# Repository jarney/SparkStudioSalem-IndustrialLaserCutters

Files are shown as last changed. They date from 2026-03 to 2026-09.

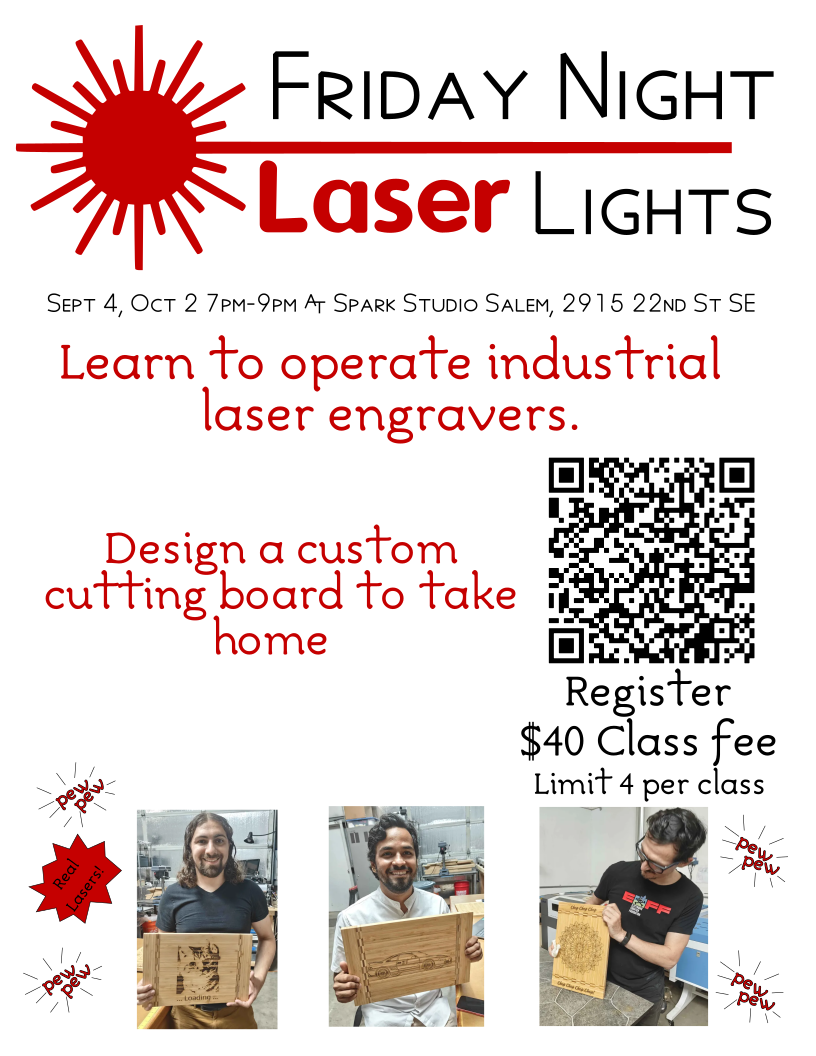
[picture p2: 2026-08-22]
promotional/FridayNightLaserLightsPromo1.png

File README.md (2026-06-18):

# Industrial 6090 150Watt CO2 Laser Cutters

This repository collects information about the Industrial
scale CO2 laser cutters at Spark Studios including
policies, safety information, training materials and technical
information such as wiring diagrams.

# Training Presentations
If you want to learn how to use the machines, there are several
presentations aimed at getting people started and certified:
* [Introduction Training](Training-GeneralPublic.pdf) and [handouts](Training-GeneralPublic-Handout.pdf): This course is intended for the general public
  to use the machines UNDER SUPERVISION of authorized users.  The nominal cost
  for this training is a $20 donation to the club.  You will learn to use the
  machine for basic cutting and engraving operations.  This is an introduction, so you
  will learn how to use the machines, but you will not yet be an expert.  This course makes use
  of some [templates](templates/svg) and a [template customization tool](https://jarney.github.io/spark/laser-cutters-6090/svg-templates/) to create
  designs for cutting during the class.

* [Authorized User Training](Training-AuthorizedUsers.pdf): This course is intended for paying members.  You will
  increase your knowledge and the focus is on ensuring safe operation and reacting to emergency
  conditions.  You will be allowed to use the machines unsupervised.

* Certifier Training (coming soon):  This course is intended for advanced users.  You will learn
  about the machine internals, alignment procedures, and more advanced topics.

# Policies and procedures

This section covers the policies and procedures for operating the machines.

* Use of these machines is governed by the [Policies](policies.pdf).
* When running jobs, please follow the [Operations Checklist](operation-checklist.pdf)
* When running jobs, please fill out a sheet in the [Operation Log](operation-log.pdf)
* Different materials should be cut and engraved with various settings.  While you may
  need to experiment to get the best results, the [Feeds and Speeds](FeedsAndSpeeds.pdf) document
  gives good starting points for common materials.
* To achieve better surface finishes, please refer to the [Pro Tips](pro-tips.pdf)
* These [Signs](signs.pdf) should be placed on the machines in event of malfunction to alert
  other users and Spark Studio board members of malfunctions.

If you wish to revise the policies, please edit the corresponding
OpenOffice (.odt) files and review with the Spark Studio Board.
Once approved, a pull-request can be sent to request that the official
copies of the policies be updated.  Note when revising policies, the
revision number and date MUST be updated in order to keep track
of which policy revision is the most recent.

# Technical Information

This section contains technical information for maintenance and
diagnosis of problems.  These are indended only for those tasked
specifically with maintaining and repairing the machines.  These
should not be used during normal operation.

This [operation manual](Gweike-operation-manual.pdf) covers
the use and operation of a similar laser cutter from Gweike.
While the laser cutters are not exactly this model, they
do give useful guidance on the machines and their operation.

The 6090 laser cutters are built using a Ruida controller
which interprets the GCode to guide the machine through making
cuts.  The [Ruida controller's documentation](RDC6445G-Control-System-V1.2-Manual.pdf)
describes more about its design and usage.

In addition, the [laser power supply has accompanying documentation](LASERPOWERSUPPLY欧规_1729590679720.pdf)
about its inputs and controls.

This [wiring diagram](laser-block-diagram.pdf) is
available for helping to understand the design of the
machines and general troubleshooting.  This diagram was produced
by reverse-engineering the design and is not authoritative,
but is as accurate as possible a diagram describing the wiring
of the machine based on its current configuration which has
been slightly altered from its original design.  The diagram is
authored in KiCad and future changes should be proposed and updated
using this format, reviewed, and implemented with the consent of
a Certifier or the Spark Studio Board.

# Modified Parts and accessories

Some parts have been designed and 3d printed in an effort to
improve the safety of the equipment.  These include:

* Spacers/stand-offs to hold a panel to prevent laser light from coming
  through the vent holes.
  
* Plugs for circular holes in front of Blue laser cutter.

* Holder for reed switch protecting the laser from firing with
  the door open.

The CAD for these files are maintained in this [FreeCAD file](LaserCutterParts.FCStd)
and printable versions can be found in the [STL](stl/) and [3MF](3mf/) directories.

# Alignment Procedures

The performance of the machines is highly dependent on how well
the machine is aligned.  Specifically, the optics must be aligned
closely with the gantry and the gantry needs to be square and parallel to
the bed.  Alignment of the machine is something of an art, but the
procedures are roughly outlined in the [Laser Alignment Guide](LaserAlignmentGuide.pdf).
These alignment procedures make use of some 3d-printed targets and
a [Laser Beam Alignment Worksheet](LaserBeamAlignmentWorksheet.svg) to assist in visualizing the beam path
and adjustments needed to bring the beam into the correct orientation.

There are beam target fixtures that can be inserted into the
apertures of [Mirror #2](stl/LaserCutterParts-P_AlignmentTarget_Mirror2.stl)
and [Mirror #3](stl/LaserCutterParts-P_AlignmentTarget_Mirror3.stl)
and affixed with blue painter's tape and marked using the [aperture](stl/LaserCutterParts-P_AlignmentTarget_ScribeAperture.stl) and [aperture](stl/LaserCutterParts-P_AlignmentTarget_Scribe.stl) marking jigs so that objective measurements can be made of beam position at each point in the beam path.

Source models for each of these parts can be found in
the [FreeCAD file](LaserCutterParts.FCStd) in case modifications to the models
are required.

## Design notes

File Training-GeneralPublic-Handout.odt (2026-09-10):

## Design:

- Open the template tool (First QR code on reverse)
- Choose a template and font.
- Use the “Customize” tab to customize to your liking.
- Preview the design to show the SVG that will be used for cutting.
- Share Design to save it as an SVG.
- Upload the SVG to the file server for cutting:

## Prepare for cutting:

- Move over to Lightburn PC
- Open Firefox and go to

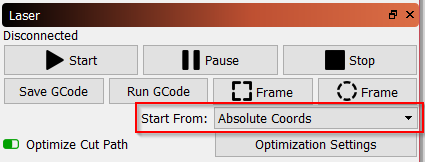
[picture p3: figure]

- http://vinyl.lan/
- Find your design in the uploads and download it to: Documents/Lightburn Projects/
- Open Lightburn from the Desktop
- File→Import, open your design from the imports folder
- Select all and align your design to X,Y at (60mm,60mm) to line it up with the jig using the icons on the toolbar.

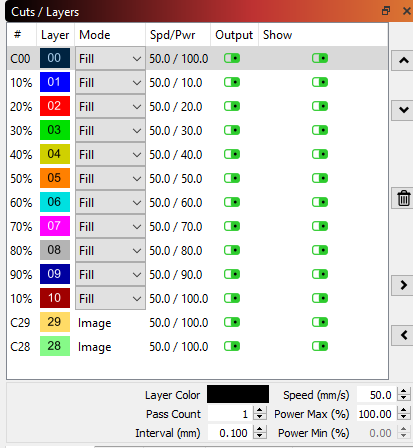
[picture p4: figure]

- Select Absolute Coordinates:
- Set the “Mode” and the “Speed/Power” for each of the colors
  - Images: Image mode, speed 250mm/s power 20%
  - Text (maroon): Fill or Line mode, speed 250mm/s power 20%
  - Lines (blue): Line mode, speed 250mm/s power 20%
  - Set the outermost line to turn off “Output”
- Confirm that “Cut Selected Graphics” is not turned on.
- Click “Send” button and give it a name (8 characters max)

## Perform the cut:

- Move over to laser cutter
- Place cutting board in jig, aligning it either “Portrait” or “Landscape” depending on your template.
- Use the “File” button and arrow keys on the laser cutter to select your file
- Press “Enter” to open up your file
- Press “Frame” button to draw the outline of your design and confirm it’s in the right place
- Confirm with your instructor that machine is ready to go (ventilation, chiller, power, air pump).
- Close door and press green “Start” button.
- Wait for machine to beep, do not leave unattended.

Other References

Other references that may be useful for making your own designs

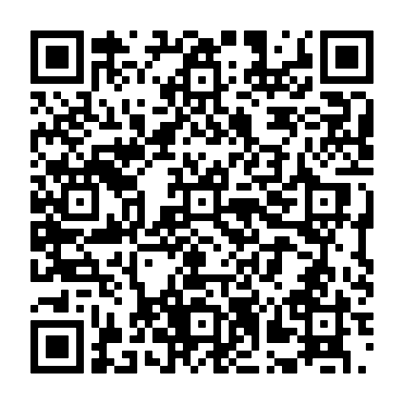
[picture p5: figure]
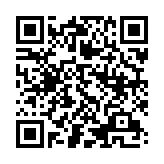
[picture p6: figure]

Spark Cutting Board Templates | Location to upload files for cutting | More Spark Studio Laser Resources

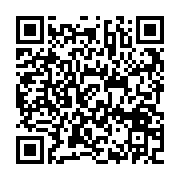
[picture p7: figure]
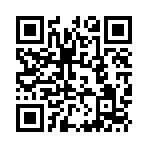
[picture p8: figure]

Inkscape Tutorials | Lightburn Tutorials

Intro to Laser Engraving (2/2)

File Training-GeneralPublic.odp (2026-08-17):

## Intro to Laser Engraving

Jon A 5/2/26

## Topics Covered

- Machine Basics
- Choose and customize a design
- Import into Lightburn for cutting
- We will set up cutter for operation
- You will laser etch your own cutting board to take home

## Machine Basics

- 150 Watt CO2 Laser (10.6um wavelength)
- Water cooled
- Adjustable bed height
- Usable Work Area: 550mm x 850mm (21.5in by 33.4in)
- Air extraction
- Air assist to improve cut quality/move debris away from nozzle

## Machine Basics

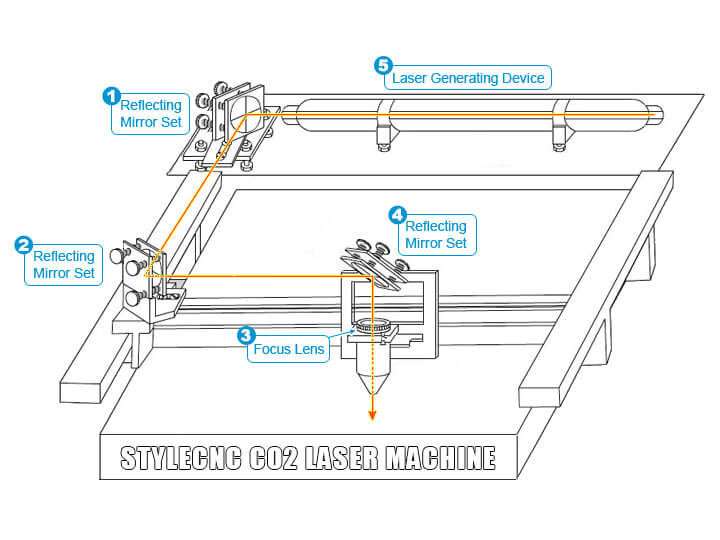
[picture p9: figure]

## Choose a template

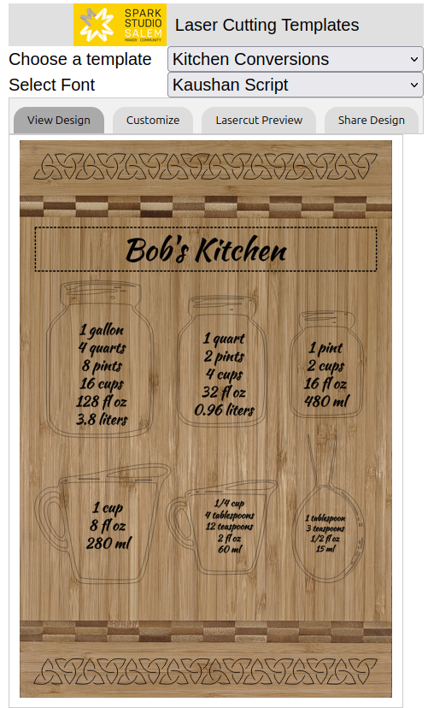
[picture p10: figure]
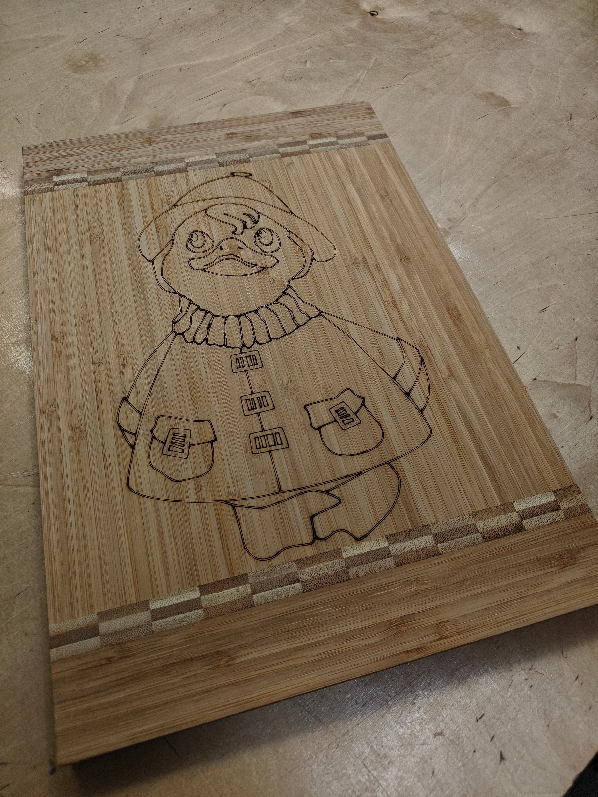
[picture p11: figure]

## Open template tool

- Select and customize file for cutting
- Download SVG file to save it
- Upload SVG file to cutting file server at:
- Lightburn for sending to laser

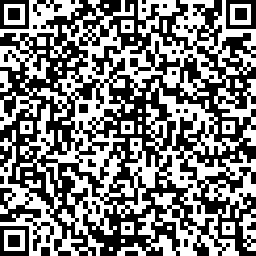
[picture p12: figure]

## Advanced Designs

- Inkscape is a great resource for more advanced designs
  - Free and open-source
- Other packages like Canva or Adobe Illustrator are suitable.
  - More expensive, but sometimes easier to use
- Great YouTube resources
- Check Handout for more information

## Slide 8

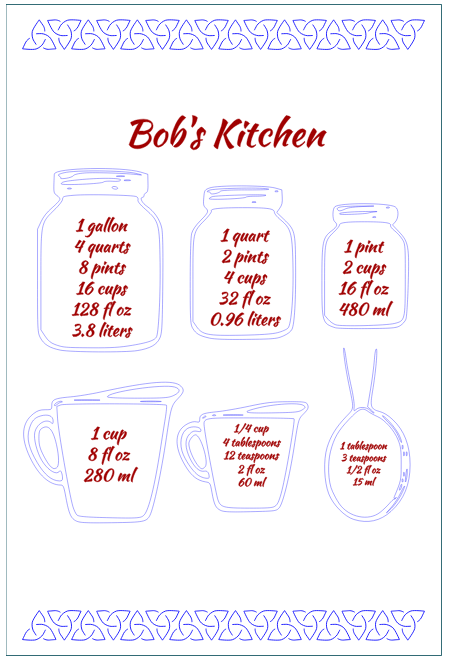
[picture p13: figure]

Finished Design

Design starts at 60mm, 60mm

Fits within the cutting board shape

Colors will be used to plan what type of operation the laser will perform.

## Import your design

- Go to Lightburn PC
- Download your SVG file
- Align design at x=60mm, y=60mm
- Matches physical location on machine

## Setting Feeds and Speeds

- Each element in your design should be given a “color”. That “color” will later determine how the cuts happen.
- Each color gets a “speed”, “power” and “mode”.
- Speed/Power determine how “deep” the laser will cut
- Mode determines how the cut is made

## Setting Feeds and Speeds

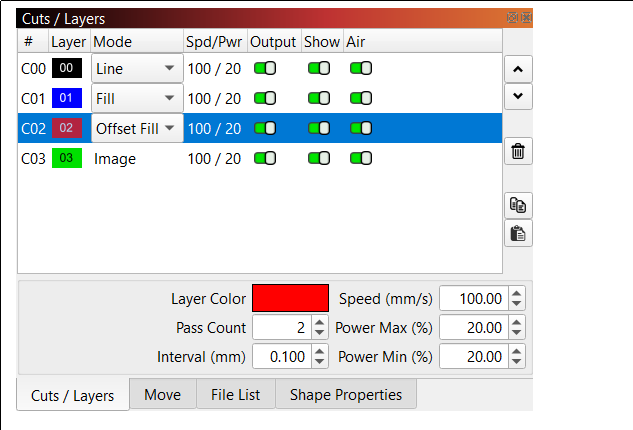
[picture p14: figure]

- Each “color” gets a speed and power, and mode
- Never exceed 50% power

## Modes

- Line: Simply follows the lines in a single pass
- Very thin lines sweeping across the design
- Good for line art and cutting shapes

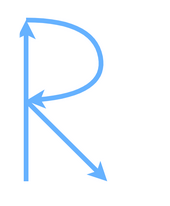
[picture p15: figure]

## Mode: Image

- Scans across the image line by line
- Pulses beam on and off to mark surface

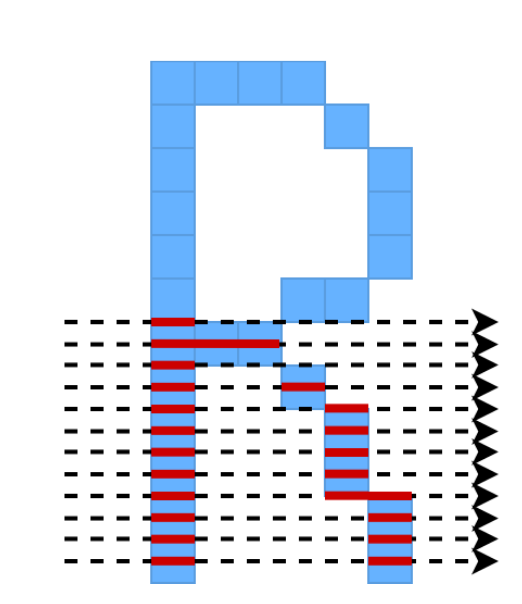
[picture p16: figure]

## Mode: Fill, Offset Fill

- Same as image, but used to fill in regions
- Offset fill doesn’t scan line by line, but instead repeatedly traces lines in concentric patterns to fill

## Material Library

- Assign layers (colors).
- Each one is a pre-set speed, power, and mode.
- Allows us to quickly determine how it will cut.
- You can still “fine-tune” speed and power afterwards if you want.

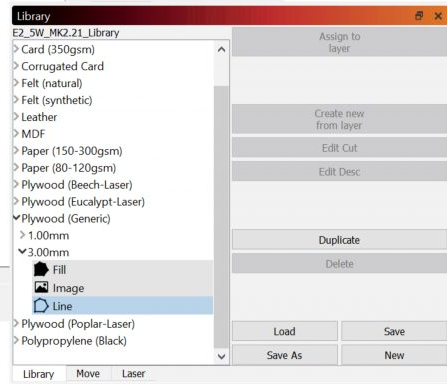
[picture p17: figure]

## Send to machine for cutting

- Once speed and power are set, we can send our design to the machine to cut it.
- SEND button
- Set “Start From” to “Absolute” coordinates


## Making the cuts

- Put material in machine
- Set focal distance between work and laser head to 5mm
- Close all doors/panels.
- Select File
- Press “Frame” button to confirm position
- Press green “Start/Pause” button.
- Don’t stare at beam
- Don’t leave unattended

## Materials

- Materials: Approved
  - MDF
  - All wood (except pressure-treated lumber)
  - Acrylic (Plexiglass)
  - UNTREATED or Vegan treated leather
  - Stone, Glass, Ceramic
  - Metal for surface engraving only
- Materials: Banned
  - Plastics containing chlorine
    - Vinyl, PVC, Nylon
  - Resins
  - Epoxies

## Safety

- Make sure all panels are closed
- Beware of fire, wood can burn.
- Beware in case lens vaporizes, possible Selenium exposure
- Do not touch mirrors or nozzle
- Persons under 18 must have parent or guardian nearby

## Next Steps

- After this training, feel free to come to the space during open-hours and use the machines provided that an authorized trainer is available to supervise machine operation. You will have to provide your own designs and materials, but use of the machines is free.
- If you become a member, there is additional training to:
  - Operate unsupervised or during non open-house hours.
  - Maintain and align machine
- If you enjoy this, we encourage you to become a member and get actively involved in the community.
- Tell your friends how much fun it is!

## Now, let’s go do some cutting!

- We will now move into the main space and make some cutting boards.
- Have fun with it and be creative.

## Next slides are just for reference

## Requirements

- Must be supervised by authorized user
- Must use only during office hours or open-house.
- 18+ or supervised by parent/guardian
- Donation to Spark
  - $40 Non-members
  - $20 Members
  - Please help us, it takes time and effort to keep these machines in good condition.
  - We also have to pay for facilities, electricity, etc.
  - You will not find a better deal anywhere!

## Trace bitmap to path

- OPTIONAL
- You can “convert” the image into a set of paths for better control
- Somewhat tricky to get the right effect, but can get really good results.
- Once it’s a path, you can edit nodes for very fine-grained control
- Works best when there’s a lot of contrast in the image

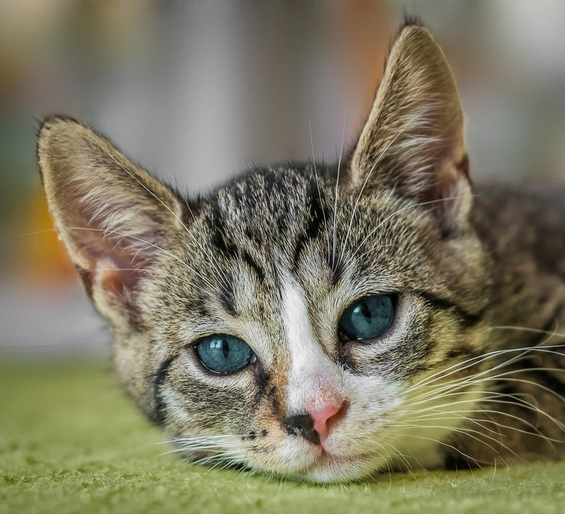
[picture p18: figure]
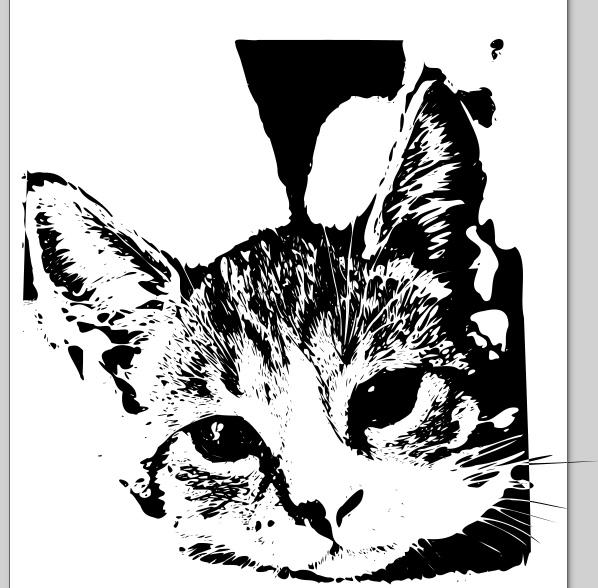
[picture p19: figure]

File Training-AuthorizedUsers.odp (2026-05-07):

## Laser Authorized User Training

Jon A 5/2/26

## Objectives

- Become an authorized user (able to use machines unsupervised)
- Learn normal operations procedures
- Learn safety procedures

## Requirements

- Must have passed “Intro” course
- Must be paying member
- Must agree to follow policy documents and checklist

## Policies

- You must carefully read, initial, and sign the policy document. This governs use of the machine and outlines your responsibility as operator.
- Copy provided by trainer
- Also available on GitHub, follow QR code on lasers.
- Policies (https://github.com/jarney/SparkStudioSalem-IndustrialLaserCutters/blob/main/policies.pdf)
- Yes, there will be a test.

## General Provisions

- Provide your own materials
- Not under influence
- Log use and failures or safety issues
- Keep machine locked when not in use
- Follow items on checklist

## Approved Materials

- If it’s not on the approved materials list, don’t cut it.
- If you disagree, get a copy of the Safety Data Sheet (SDS) and appeal to board for changes to policy, we can change if presented with a well-reasoned argument.

## Safety:

- Each type of safety condition should be handled depending on its nature.
  - Fire
  - Lens Vaporization
  - Tube Malfunction

## Fire

- Most common
- Not a problem if handled quickly
- Big problem if left unattended
- Use E-Stop
- Extinguish fire, escalating as needed
  - Turn off air assist
  - Use fire blanket
  - Use extinguisher
  - Call 911
- Log failure and notify board.

## Lens Vaporization

- Prevent by examining lens about monthly to make sure residue hasn’t accumulated. If you don’t want to clean it yourself, notify someone who can.
- Prevention is the most powerful tool here.
- Lenses cost ~$40 and it’s much easier, safer to replace a lens than to clean the machine.
- Keep lid closed
- Keep locked
- HAZMAT to avoid Selenium exposure
- Log failure and notify board
- Place sign on machine to warn of exposure.

## Laser tube malfunction

- Tube can crack
  - Physical shock
  - Water freezing
- High-voltage risk
- E-stop
- Log failure, notify board member
- Keep locked, closed
- Sign on machine

## Supervising others

- You may supervise general public WHO HAVE HAD INTRO TRAINING
  - We encourage this because it may help drive membership and donations
- You must watch them and stay nearby
- You are ultimately responsible for safety

## Demonstrate Safe Operation

- We will now go to the lasers and
  - Prepare them for use
    - Unlock machine
    - Exhaust vents
    - Fan power
    - Air assist
    - Chillers

## Demonstrate Safe Operation

- We will now go to the lasers and
  - Cut a small job
    - Focal length
    - Lightburn settings

## Demonstrate Safe Operation

- We will now go to the lasers and
  - Close them down
    - Lock machine
    - Exhaust vents
    - Fan power
    - Air assist
    - Chillers

## Examination

- Be prepared to answer questions about what to do in case of emergency
  - Fire
  - Lens vaporization
  - Tube malfunction

## Congratulations, you are now authorized

- Signoff
- Authorized user badge/token

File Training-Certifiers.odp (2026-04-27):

## Laser Certifier Training

Jon A 5/2/26

## Objectives

- Become a certifier
- Basic machine maintenance and diagnosis
- Deliver training
- Sign off on unsupervised use
- Question and “examine” candidates to make sure they understand safety.

## Requirements

- Must be a paying member
- Must agree to supervise and be responsible for use

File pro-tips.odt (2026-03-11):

Industrial Laser Cutter

Pro Tips

This is not an exhaustive list, but there are a few tips for achieving a better surface finish. Some experimentation may be required, but a quite good surface finish is possible with some setup and care.

Cast acrylic leaves a better surface finish and less deformation than extruded acrylic. If surface finish is important, use cast acrylic.

Higher pressure air assist removes residue from work piece more efficiently and leaves a better surface finish with less post-processing. If available, using an air compressor to feed the air assist will provide a better surface finish.

Flashback (reflections from the holders that scar the back of the work piece) can cause residue to form on the back/bottom of work piece. Consider using the “Slats” or a “pin bed” to hold the work piece in order to reduce flashover and leave a better surface finish on back.

When etching glass, the 150W lasers are usually too powerful. Use a low power setting and consider de-focusing the beam slightly. Also, applying a thin layer of dilute dish soap to work piece to facilitate cleaning of small glass particles formed during etching process.

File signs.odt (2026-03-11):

WARNING!

LASER HEAD IN NEED OF ALIGNMENT

HAZARD!

LENS VAPORIZATION

POTENTIAL SELENIUM EXPOSURE

DO NOT OPEN CABINET WITHOUT PPE

HAZARD!

LASER TUBE MALFUNCTION

POTENTIAL HIGH-VOLTAGE ELECTRICAL DISCHARGE

HAZARD!

MACHINE HAS EXPERIENCED UNCONTROLLED FIRE AND IS IN NEED OF MAINTENANCE

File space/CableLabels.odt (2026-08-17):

Network Cables

5G Router

Internet Ingress

See Network Diagram

5G Router to SW1

SW1

Ethernet Switch

See Network Diagram

SW1 to 5G Router

SW1 to SW2

Access Point 1

See Network Diagram

Access Point 1 to SW1 (PoE Port)

Access Point 2

See Network Diagram

Access Point 2 to SW2 (PoE Port)

SW2

Ethernet Switch

See Network Diagram

SW2 to SW3

SW2 to Access Point (PoE Port)

SW3

Ethernet Switch

See Network Diagram

SW3 to SW2

SW3 to Gweike Laser

SW3 to Blue Laser

ROUTER2

Internal Network

172.16.0.1 (hostname router)

See Network Diagram

Username: admin

Password: password

DHCP/DNS Server

172.16.0.2 (hostname dns)

OS Username: spark

OS Password: OS6and7

pihole password: OldSchool6and7s

DHCP Range: 172.16.0.100-172.16.0.254

Vinyl Cutter

172.16.0.3 (hostname vinyl)

Inkcut server for vinyl cutting using SVG

DNS Labels:

host:3dprint-octoprint1

ip:172.16.0.11

host:3dprint-qidi

ip:172.16.0.10

host:conference-roku

ip:172.16.0.81

host:digitalarts-inkjet-epson409961

ip:172.16.0.53

host:digitalarts-pc1-windows

ip:172.16.0.51

host:digitalarts-pc2-linux

ip:172.16.0.52

host:digitalarts-tshirt-power-tapo

ip:172.16.0.54

host:frontoffice-camera-wyse

ip:172.16.0.73

host:frontoffice-door-august

ip:172.16.0.191

host:frontoffice-pc

ip:172.16.0.71

host:frontoffice-windowbox

ip:172.16.0.70

host:frontoffice-printer

ip:172.16.0.72

host:laser-cutter-airsensor-electricimp

ip:172.16.0.25

host:laser-cutter-crackle

ip:172.16.0.23

host:laser-cutter-particlesensor-electricimp

ip:172.16.0.21

host:laser-cutter-pop

ip:172.16.0.24

host:laser-cutter-snap-glowforge

ip:172.16.0.22

host:laser-cutter-vinyl

ip:172.16.0.3

host:loft-camera-wyse

ip:172.16.0.91

host:loft-xbox-david-duncan

ip:172.16.0.90

host:network-accesspoint1-loft

ip:172.16.0.30

host:network-accesspoint2-3dprinting

ip:172.16.0.31

host:network-switch-netgear-gs728tp

ip:172.16.0.32

Breaker Labels

Breaker: B1 : Northwest Warehouse Plugs

Breaker: B3 : Bathroom

Breaker: B3 : Bathroom

Breaker: B3 : Bathroom

Breaker: B5 : Warehouse Heater

Breaker: B7 : Loft lights and network

Breaker: B9 : South Wall Plugs

Breaker: B11,B13 : 220VAC Under breaker panel

Breaker: B15,B17 : Mini-split AC unit

Breaker: B19 : Conference room

Breaker: B19 : Conference room

Breaker: B19 : Conference room

Breaker: B19 : Conference room

Breaker: B21 : East Wall “Pop” (Blue&White Laser cutter)

Breaker: B23 : East Wall “Crackle” (Gweike)

Breaker: B25 : Northeast Wall 3d printers, “Snap” GlowForge

Breaker: B27 : East Wall Electronics Bench

Breaker: B2 : Warehouse Lights

Breaker: B4, B6 : Water Heater

Breaker: B8 : Overhead Power Drop

Breaker: B10 : Outside Lights

Breaker: B12,B14 : Do not turn off/ Unknown(?)

Breaker: B16,B18 : Bathroom Heater

Breaker: B20,B22,B24 : Laser Exhaust Fans

Breaker: B26,B28,B30 : Air Compressor Panel

# PC Labels

General Purpose PCs

For use in training programs and general public:

Ubuntu 24.04LTS

Password: OS6and7

Loaded with:

Inkscape

Lightburn

Gimp

FreeCAD

A bunch of fonts

Please speak with Jeremy G, Jon A, or Rike S before making modifications

Please return to loft shelf when finished

Monitor for General Purpose PC

General Purpose PCs

Anyone may use these for training or general use.

Please return to this location when you are finished using them.

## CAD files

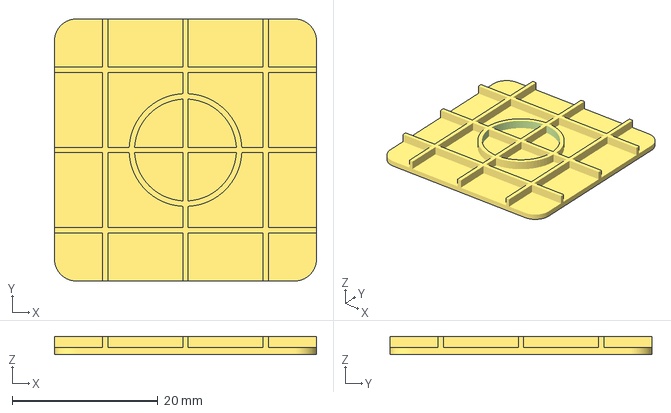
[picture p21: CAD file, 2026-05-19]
3mf/StampSurface.3mf
36.0 x 36.0 x 2.50 mm

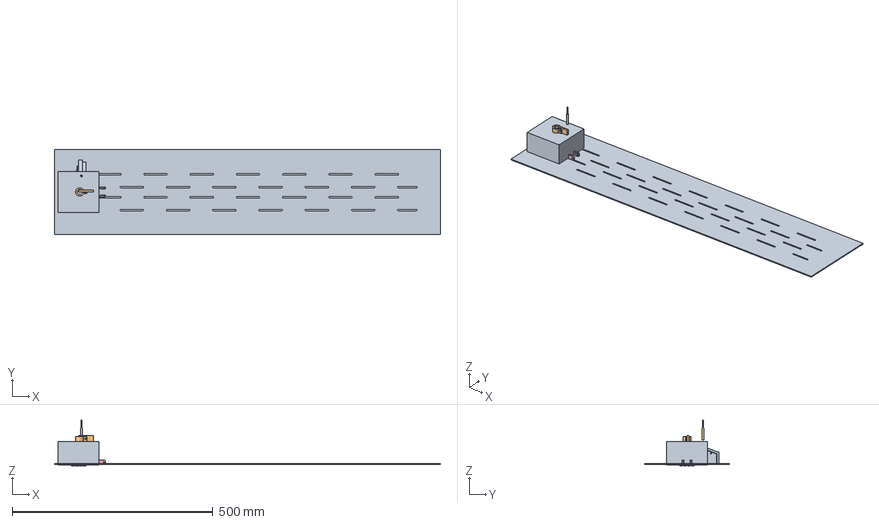
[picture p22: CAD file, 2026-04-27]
LaserCutterParts.FCStd
961.4 x 211.8 x 114.3 mm
B_FrontPanel
B_FrontPanelBaffle_Spacer
B_FrontPanelBaffle_Endcap
B_LimitSwitchSpacer
B_HolePlug_FrontPanels
B_HolePlug_Tester
B_ReedSwitch_Magnet
B_ReedSwitch_Holder
B_Cabinet_Body
B_Cabinet_Lid
B_ReedSwitch
B_CAMTest
B_TPLinkBracket_Right
B_TPLinkBracket_Left
B_AlignmentWrench1
B_AlignmentWrench2
B_AlignmentTarget_Mirror3
B_AlignmentTarget_Mirror2
B_HolePlug_SidePanels
B_AlignmentTarget_Stamp
B_AlignmentTarget_Scribe
B_IndicatorMount
B_AlignmentTarget_ScribeAperture
B_AlignmentTarget_HeadTube
B_AlignmentTarget_HeadTarget
B_LaserPointerMount
B_LaserPointerMountAperture
B_AlignmentTarget_Gweike_Mirror3
B_IndicatorMount2
Model-P_CAMTest
CutTool
SHAPESTRING_AlignmentTarget_Mirror3_Label001
Stock
5mm Endmill

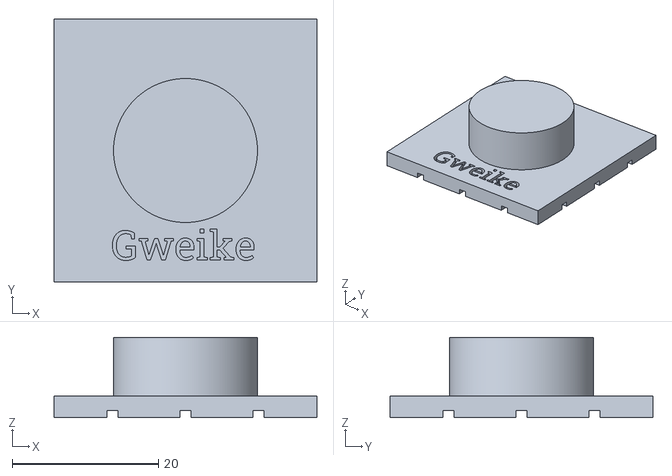
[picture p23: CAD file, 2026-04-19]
stl/LaserCutterParts-P_AlignmentTarget_Gweike_Mirror3.stl
36.0 x 36.0 x 11.0

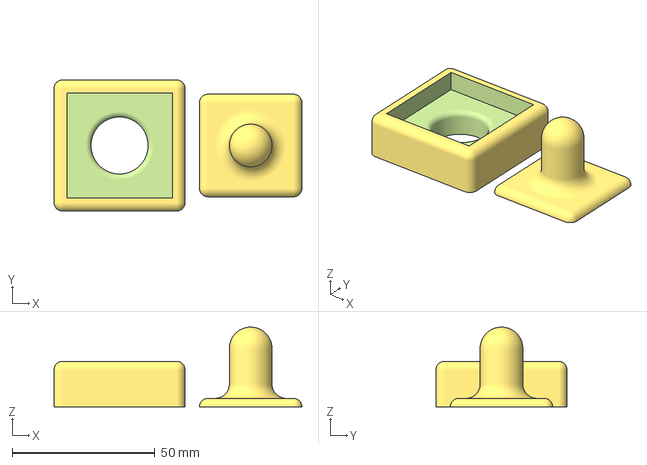
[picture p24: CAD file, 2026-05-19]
3mf/AlignmentStamp.3mf
87.0 x 46.0 x 28.0 mm

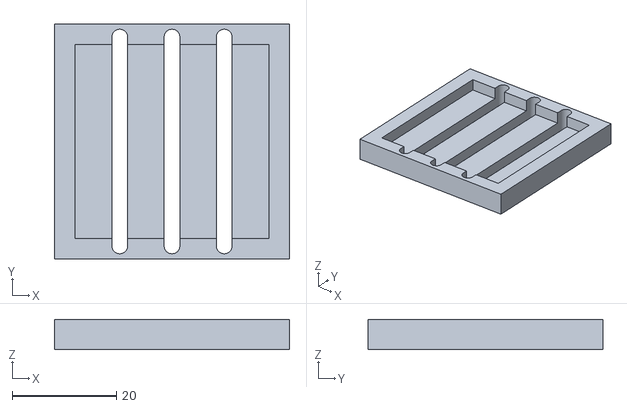
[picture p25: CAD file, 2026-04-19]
stl/LaserCutterParts-P_AlignmentTarget_Scribe.stl
45.0 x 45.0 x 5.80

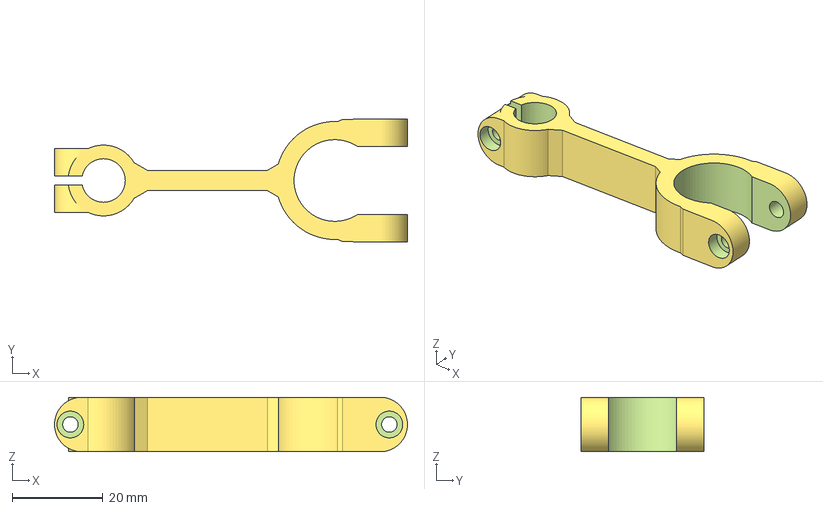
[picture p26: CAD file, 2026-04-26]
3mf/dial_holder.3mf
77.8 x 27.0 x 12.0 mm

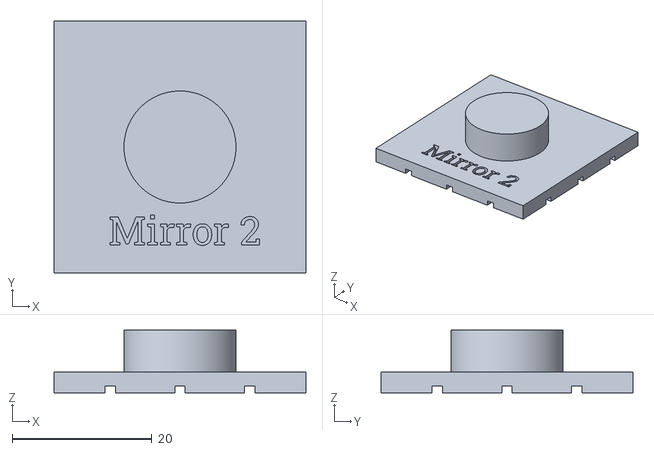
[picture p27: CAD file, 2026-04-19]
stl/LaserCutterParts-P_AlignmentTarget_Mirror2.stl
36.0 x 36.0 x 9.00

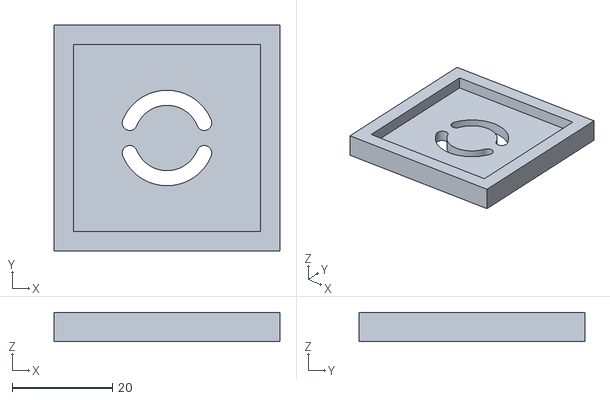
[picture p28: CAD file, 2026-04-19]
stl/LaserCutterParts-P_AlignmentTarget_ScribeAperture.stl
45.0 x 45.0 x 5.80

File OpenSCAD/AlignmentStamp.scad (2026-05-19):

include<BOSL2/std.scad>

shell = [46,46,16];
disc = [10,undef,8];
plate = [37,37,shell.z];
stamp = [36,36,1];
aperture = 14;
$fn = 72;

/* [Select] */
part = "set";  // [base, handle, set, stamp,set]

if (part == "base")   {base();}
if (part == "handle") {handle();}
if (part == "set")    {left(shell.x/2) base(); right(shell.x/2) handle();}  
if (part == "stamp")  {stamp();}   // print with softest available tpu


module base() {
    diff() {
        cuboid(shell, rounding = 3, except = BOT, anchor = BOT) {
            tag("remove") position(BOT){
                up(disc.z+1) cuboid(plate, anchor = BOT);
                cyl(h = disc.z+1.01, r = disc.x, rounding2 = -2, anchor = BOT);
            }
        }
    }
}

module stamp() {
    cuboid(stamp, rounding = 3, edges = "Z", anchor = BOT)
        position(TOP){
            xcopies(n=3, spacing = 11) cuboid([0.75,stamp.y,1.5], anchor = BOT);
            ycopies(n=3, spacing = 11) cuboid([stamp.x,0.75,1.5], anchor = BOT);
            tube(id = aperture, wall = 0.75, h = 1.5, anchor = BOT);
        }
}

module handle() {
    cuboid([stamp.x, stamp.y, 3], rounding = 3, edges = ["Z",TOP], anchor = BOT)
        position(TOP) cyl(h = 25, d = 15, rounding1 = -5, rounding2 = 7.5, anchor = BOT);
}

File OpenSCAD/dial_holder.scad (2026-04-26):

/*  Dial holder for Blue_6090 Industrial Laser Cutter Alignment
    Printing from Carbon or Glass Fiber filled filament recommended.
*/


include <BOSL2/std.scad>
include <BOSL2/screws.scad>

$fn = 72;
wall = 3;
zdim = 12;   // Overall height
d1 = 9.6;    // Dial Indicator Clamp Dia.
d2 = 18;     // Lens Barrel Clamp Dia.
bridge = [50-d1/2-d2/2-2*wall+2, 1.5 * wall, zdim];

holder();

module holder() {
    diff() {
        // Dial Indicator Clamp
        tube(id = d1, wall = wall, h = zdim, anchor = BOT){
            position(BOT) tag("remove") cyl(h = zdim, d = d1, anchor = BOT);
            position(LEFT) right(2*wall) cuboid([3*wall,4*wall+2,zdim], rounding=zdim/2, edges="Y", except=RIGHT, anchor=RIGHT){
                position(FWD) left(1) tag("remove") screw_hole("M3", l = 2*wall, head = "socket", anchor = TOP, orient=FWD);
                // Sized for m3 heat-set threaded insert
                position(BACK) left(1) tag("remove") ycyl(d = 4, l=2*wall, anchor = BACK);
            }
            position(LEFT) tag("remove") cuboid([4*wall, 2, zdim]);
            // Connecting Bar
            position(RIGHT) left(1) cuboid(bridge, anchor = LEFT){
                //End fillets
                align([LEFT,RIGHT], inside = true) tag("keep") left(wall*3/4+$idx*1.5*wall) zrot($idx*180) cyl(d = 3*wall, h = zdim, anchor = BOT, $fn = 3);
                // Lens Barrel Clamp
                position(RIGHT) left(1) tube(id = d2, wall = wall+1, h = zdim, anchor = LEFT){
                    position(BOT) tag("remove") cyl(h = zdim, d = d2, anchor = BOT);
                    align(RIGHT, inside = true, shiftout = 3) tag("remove") cuboid([4*wall+3,15,zdim+1]);
                    position(RIGHT) left(3*wall) cuboid([4*wall,15+4*wall,zdim], rounding= zdim/2, edges="Y", except=LEFT, anchor=LEFT){
                        align([BACK+LEFT, FWD+LEFT], inside = true, shiftout = -0.2) tag("keep") left(3) xscale(4) cyl(h = zdim, d = 1.4, $fn=6);
                        position(FWD) right(2) tag("remove") screw_hole("M3", l = 20, head = "socket", anchor = TOP, orient=FWD);
                        // Sized for m3 heat-set threaded insert
                        position(BACK) right(2) tag("remove") ycyl(d = 4, l=2*wall, anchor = BACK);
                    }
                }
            }
        }
    }


}

 //left(10) fwd(50) zrot(90) ruler();

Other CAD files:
stl/LaserCutterParts-P_AlignmentTarget_Mirror3.stl

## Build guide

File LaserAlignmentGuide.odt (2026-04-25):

Outline of procedures to align the gantry, optics, and bed

# Introduction

The performance of these laser cutters is highly dependent on how well the machine is aligned and calibrated. The alignment of the machine is something of an art and requires patience and understanding of the fundamentals of optics. Fortunately, if inspected regularly, the full procedure is rarely needed. This document contains an outline of the main alignment procedures and also a monthly maintenance guide. Once aligned, the machine should be maintained by following the monthly inspection process to verify that the machine is still adequately aligned and perform minor adjustments as needed. This is intended to ensure that the full alignment process is needed only rarely and that most of the time, only minor adjustments are needed to keep the machine in working order.

# Alignment Procedure Outline

## 1. Gantry Skew

In this stage, we aim to align the gantry so that the left and right rails are parallel. Using a bubble-level, check that each of the rails is angled from front-to-back by the same amount. If necessary, the entire machine can be trammed so that they are both level as closely as possible. Note that precise alignment is not necessary, but try to get the left and right rails within about 1 degree of the same angle front-to-back. The height of the front anchor point of each of the rails can be adjusted by loosening the screws holding the Y axis rails to the chassis and moving them higher or lower. Continue iterating on this until they are as close to parallel as you can make them. [Ref 1].

This is not too crucial for the optics because mirror #2 rides along the rails. Any “skew” in the yz plane will be washed out because the mirror moves with the rail. Nonetheless, make an effort to ensure that the rails are as level as possible in reference to one another.

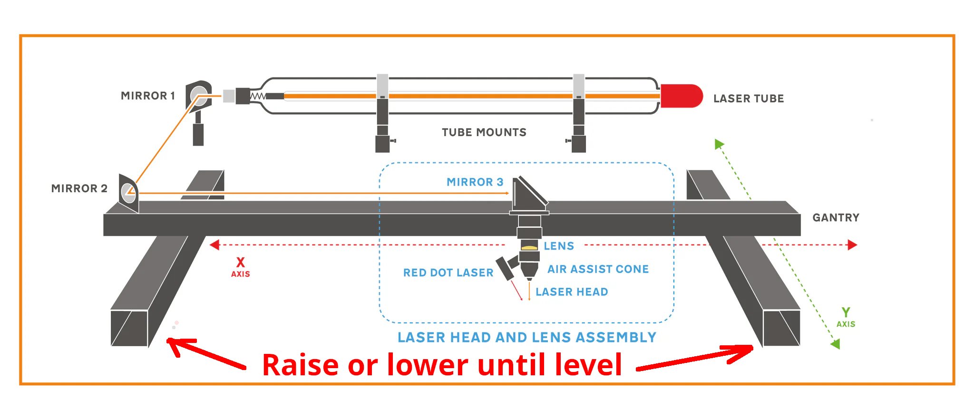
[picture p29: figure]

Measuring gantry skew. In order to check the gantry for skew, use a piece of fine thread stretched taught on the two diagonals of the gantry rails. If the gantry is square in the YZ plane, the two threads will intersect at the center. If one is higher or lower, then the rails are not perfectly parallel. Raise or lower the gantry until the two threads are just barely touching. You can secure the thread at each end with magnets or tape so they remain tight while making adjustments. Make sure to remove the thread after adjustment.

## 2. Gantry Mirror Interference

It sometimes happens that mirror #2 mounted on the gantry is accidentally bumped by the drag chain, cables, or other impediments. It only takes a microscopic deflection to move the mirror and thus beam spot at the far end of the machine. Take care to ensure that the cables, drag chain, and other moving parts do not bump or interfere with the free motion of the mirror mounted on the gantry.

## 3. Bed Leveling

In this stage, we aim to ensure that the XY plane of the bed is parallel to the XY plane of the gantry. The easiest way to do this is to place a large rigid, square object on the bed. Ideally, this object should be a) flat b) rigid, and c) cover the entire bed.

Next, jog the laser head to each of the 4 corners and use a small flat object to move the laser head so that the lowest of the 4 corners just touches the object. Our aim from here will be to adjust the z-axis lead screws so that all 4 corners match. To adjust one of the lead screws, use a hex wrench to loosen the set screw for the sprocket for that lead screw and manually adjust the lead screw until it just touches the object or the dial indicator reads the correct height. Re-tighten the set screw for the sprocket to lock the position in place. Continue this process until all 4 corners read the same height in reference to the tip of the laser tube.

For extra precision, a dial indicator can be mounted on the laser lens tube. Once done, the laser head can carefully be moved around the bed to measure how much deviation there is across the bed. A good alignment should yield something on the order of 10 thousandths of an inch (0.254mm)

This image depicts using a dial-indicator mounted on the laser lens aperture to measure relative height of the bed against the plane of the gantry. Note that the indicator SHOULD NOT BE MOUNTED UNTIL THE CONTROLLER HAS BEEN TURNED ON AND HOMED. You don’t want the indicator to be dragged by the controller over the bed during homing as this can damage the indicator and possibly crash the head.

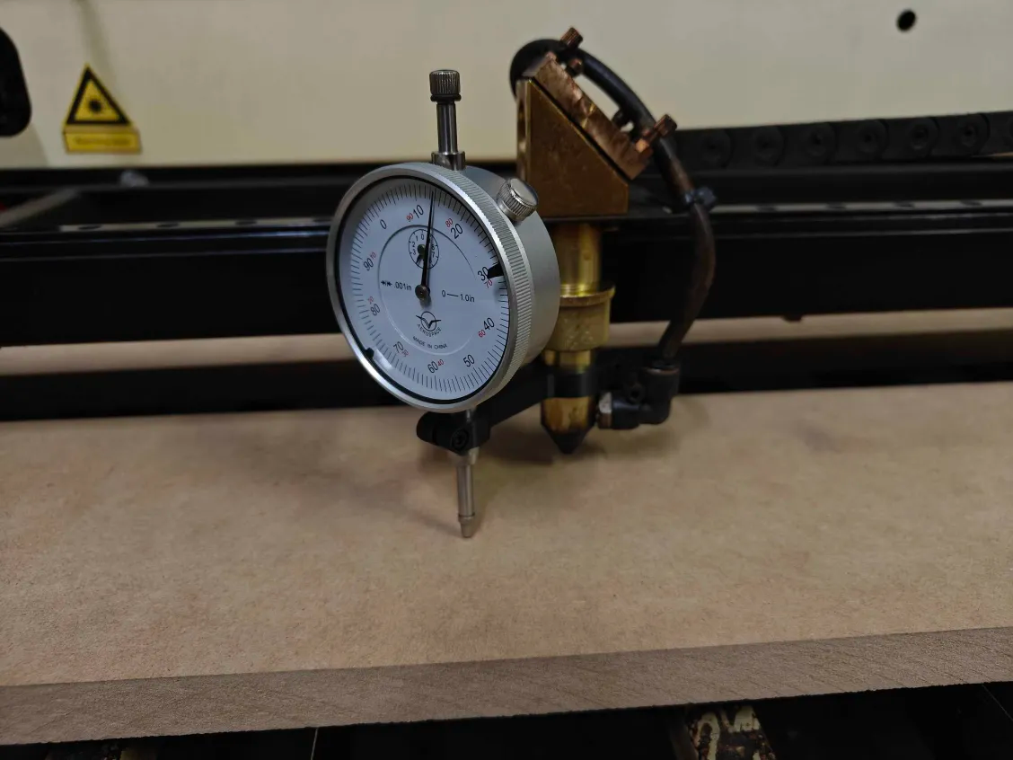
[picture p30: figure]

Once the indicator can measure the height in different locations, the bed can be adjusted carefully to raise or lower the corners until the bed and gantry are in the same plane.

[Ref 2]

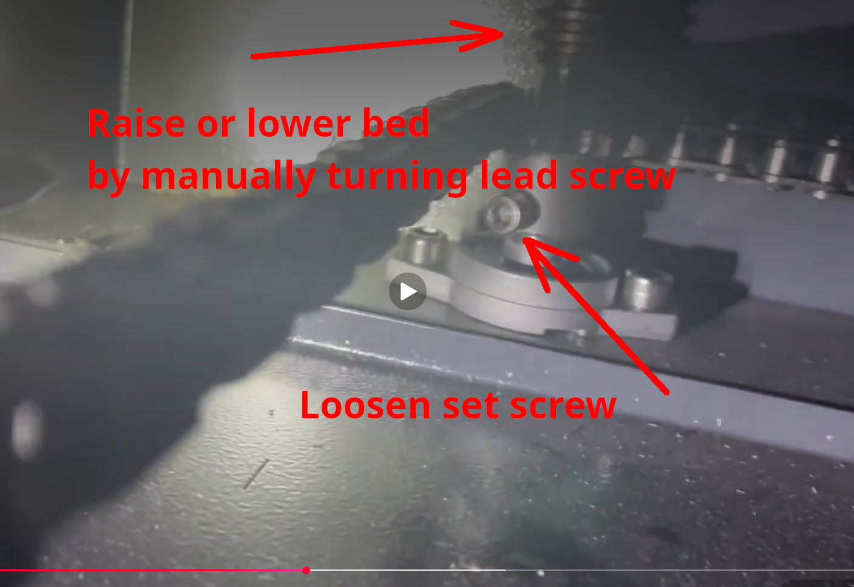
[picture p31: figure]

## 4. Tube Adjustment

In this stage, we aim to ensure that the laser beam arrives at mirror #1 in the center of the aperture. In order to do this, it may be necessary to shim the laser tube or make fine adjustments to the tube location until the beam arrives at the center as parallel as possible. Note that it is difficult to ensure that the tube is exactly perpendicular to the aperture because there is only a very small gap between the end of the laser tube and the aperture, but align it as closely as possible with the naked eye. Alignments of the mirrors will make up for small deviations from the correct angle.

## 5. Mirror 1 Adjustment

In this stage, we aim to ensure that the laser beam arrives at mirror #2 at the center of the aperture.

Place a piece of blue painter’s tape over one of the “Mirror 2 Target”, mark the grid and aperture location with a pen using the accompanying templates. These markings will assist in objectively knowing the position of the test pulse in reference to the aperture and a 10x10mm grid.

Then, place the target in the input aperture of mirror #2. Close the lid and power on the laser. Fire a test pulse at 10% power with the laser head in the upper-left corner of the bed (closest to the laser head). Repeat this process in the lower-left corner. If the pulses arrive in different locations, carefully adjust the set-screws on mirorr #1 for the up/down and left/right to move the beam in the desired direction. Note that when adjusting the mirror, the one in the “lower” corner will move a larger distance than the one in the “upper” corner. Repeat this adjustment until both pulses arrive in the approximate center of the aperture and as close to one another as possible.

Note that after aligning mirror #2, it may be necessary to further adjust mirror #1, but this should be the approximate starting location for further alignment.

## 6. Mirror 2 Alignment

In this stage, we aim to ensure that the laser beam arrives at mirror #3 (the mirror on the laser head) in the exact center of the aperture consistently all the way across the bed.

Place a piece of blue painter’s tape across one a “Mirror 3 Target” and mark the grid and aperture location with a pen using the accompanying templates. These markings will assist in objectively knowing the position of the test pulse in reference to the aperture and a 10x10mm grid.

Then place the target in the input aperture of mirror #3. Jog the laser head to the upper-left corner of the bed. Fire a test pulse at 10% power. Repeat this for each of the 4 corners. It is sometimes helpful to save these pulses by sticking them to a copy of the “Laser Alignment Worksheet”. This will give the location of the pulses on each of the 4 corners of the bed.

Adjusting the set-screws on mirror #2 will move each of those pulses up and down or left and right. Note that there will be more movement of the beam on the right side than the left, but the motion of them should be approximately the same. For example, if the upper-right and lower-right test spots are both 4mm high, you would want to adjust mirror #2 downward. Doing this would move both the upper-right and lower-right spots downward by the same amount. It is usually not the case that they will move in different directions or by different amounts.

Also note that the right side spots will move more than the left-side spots. This is because the left-side spots are a very small distance from mirror #2 than the right-side spots.

Begin the adjustment by carefully adjusting the “left/right” screw until all 4 spots are as close to the center as possible and cluster around it. For example, if they’re not quite aligned, you goal would be to put one spot slightly to the left and the other slightly to the right. Once the left/right is approximately on center, proceed to the “up/down” adjustment.

Again, for the “up/down” adjustment of mirror #2, you should aim to get all 4 spots as close to the center as possible. If they’re not quite aligned, you should aim to get them evenly distributed above/below so that “on average” they’re in the same location.

If the 4 test spots are within about 1-2mm of center, that is usually sufficient. If so, skip to step 8. If not, it may be required to re-adjust mirror #1 (Step 6) and then come back to mirror #2 (Step 5).

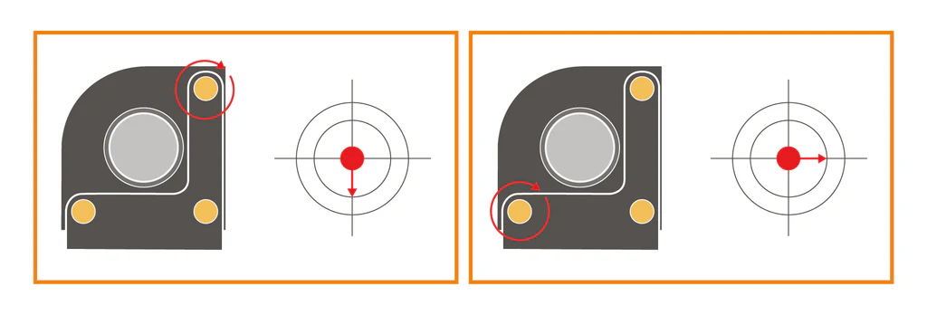
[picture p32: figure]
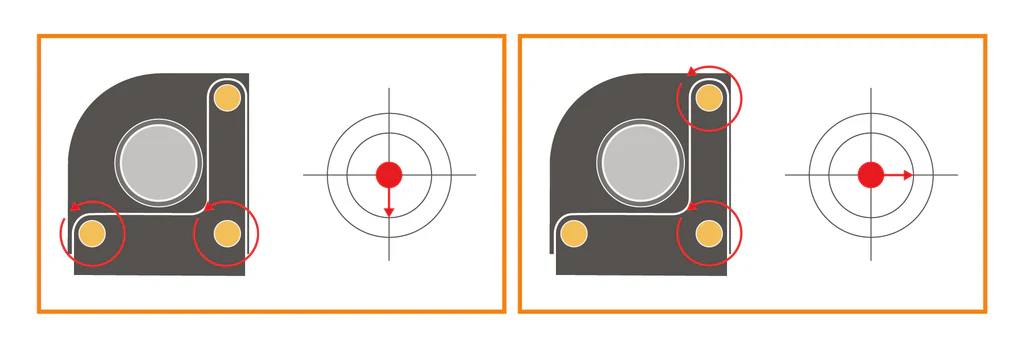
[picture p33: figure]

[Ref 1]

## 7. Mirror #1 fine-tuning

Because adjustment of mirror #2 will move the spots on the right side (furthest from the mirror) by approximately the same amount, mirror #2 usually cannot compensate for the fact that the right-side spots are not consistent from front to back of the machine. This is because the beam length traveled and mirror angle are the same for these locations. In order to adjust the location of the spots relative to one another, it will be necessary to very slightly adjust mirror #1. This is because the length of the path from the upper-right to mirror #1 is shorter than the length of the path from the lower-right to mirror #1.

The goal of this alignment is to VERY SLIGHTLY alter the direction of the beam until the spots in the upper-right and lower-right hit at the same location EVEN IF THEY ARE NOT IN THE CENTER. Centering these spots will be done by returning to step 5. where both can be moved at the same time using mirror #2. This alignment only aims to make sure that the amount they of off by is the same.

Return to step 5 to re-center the spots. Note that after this fine-tuning adjustment, the spots from the original mirror #1 alignment may no longer arrive at the exact center of the aperture. This is ok as long as the spots arrive at the center of mirror #3 consistently across the bed.

## 8. Mirror #3 alignment

The goal of this stage is to ensure that the beam arrives at the center of the lens. There is no alignment target for this, so adjustment will have to be done without a specific target.

Remove the lens from the laser head and place a piece of blue painter’s tape on the bottom. Score or mark the painter’s tape so that the aperture can be judged. Fire a test pulse to mark the painter’s tape. Carefully adjust the set-screws on mirror #3 and repeat this process until the spot arrives as close as possible to the center of the output aperture (where the lens will be).

Once this is done, place a piece of tape on the bed and fire a test-pulse. Move the bed to its lowest position and fire another test-pulse. Continue adjusting mirror #3 until the two pulses (highest Z to lowest Z) arrive are at the same location. This process ensures that the beam is aligned so that it is perfectly perpendicular to the work surface.

## 9. Gantry Square

The goal of this step is to make sure that the gantry is truly square. This must be done after step 7 because it relies on having a consistent beam all across the bed in order to mark a square.

Perform a test etch on a piece of material as large as possible. The test etch should be done at low power (~15%) and high speed (~200mm/s). The test pattern should be a large rectangle with lines across the two diagonals [Ref 3].

With these two diagonals marked on the large workpiece, measure the length of the diagonals carefully. If you find one of them significantly longer than the other, you should square the gantry. If they are the same length then the gantry is already square.

In order to adjust the gantry square, disengage the set-screws that tie the left side and right side of the gantry cross-member so that they move independently. The gantry cross-member can then be carefully moved clockwise or counter-clockwise by a few degrees. VERY SLIGHTLY adjust the angle of the gantry cross-member and repeat the rectangle and diagonals test. Repeat until the lengths of the two diagonals match.

Note that in the process of adjusting the diagonals, it may be necessary to return to the mirror adjustment stage, so repeat the test marks from steps 5-7 to confirm that the beam is still centered in the aperture and perpendicular to the work surface at the end.

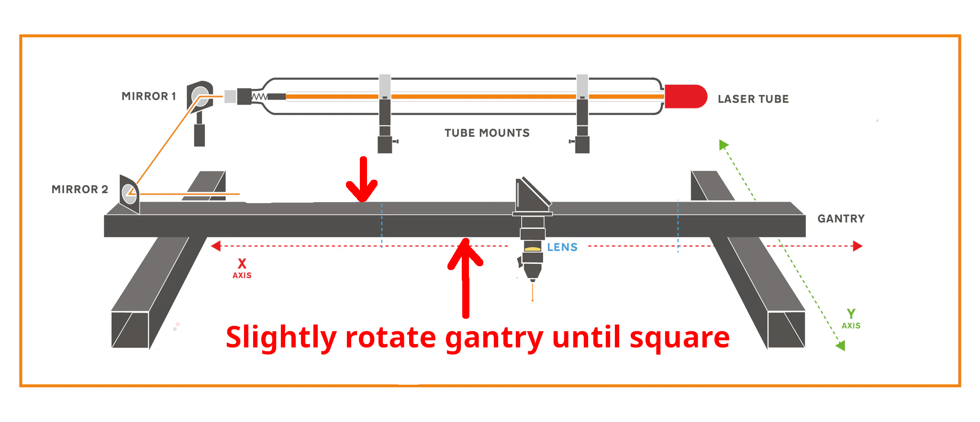
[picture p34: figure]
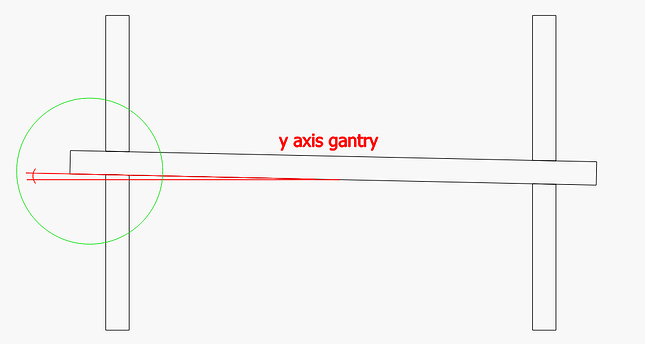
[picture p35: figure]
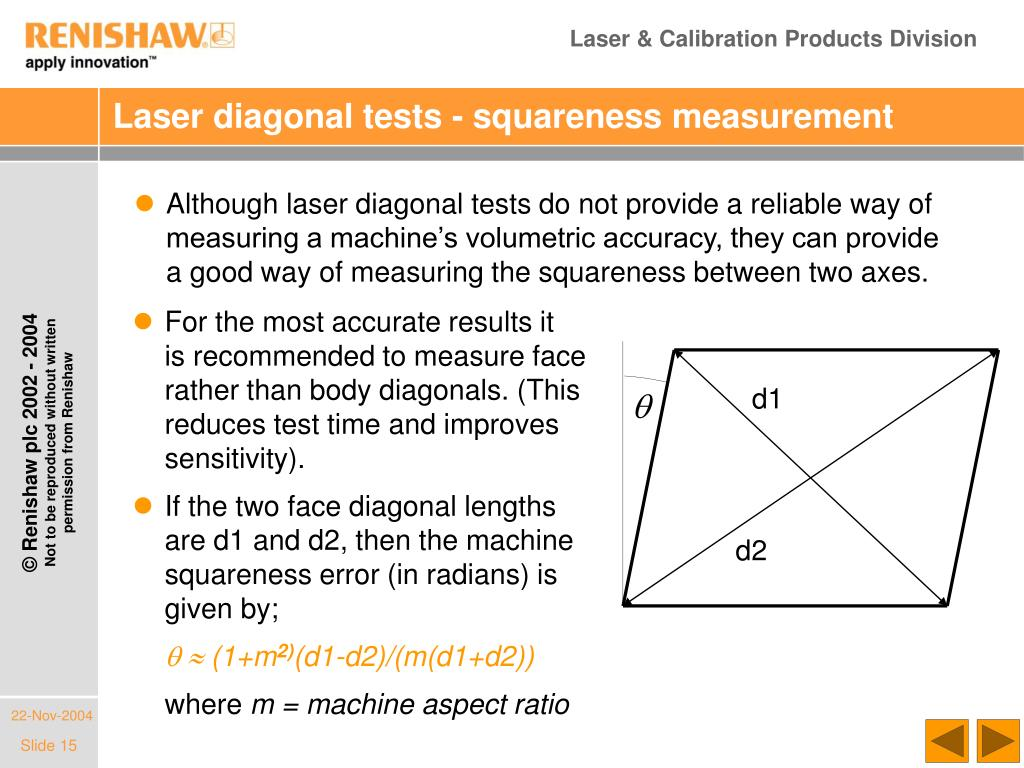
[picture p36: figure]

Rather than marking an entire rectangle, it suffices to mark 4 spots at each corner of the bed. This can be done inexpensively by fixing a small piece of cardboard or other sacrificial media at each corner of the bed. The laser can then be test-fired and the diagonal corners can be measured. This avoids the cost of using a very large sacrificial test piece to mark. The only thing that is important is that the points are marked and don’t move between the time they are marked and the time they are measured.

# Lens Maintenance

In order to cut efficiently and safely, the lenses should be cleaned regularly. If debris does not come off from lenses during cleaning, they should be replaced. Spares are located in the cabinet on the west wall in the tub marked “laser supplies”.

## Cleaning Procedure

Lenses should be cleaned as follows:

- Wear gloves to prevent contamination and body oils from being deposited on the lenses. They also protect the wearer from possible Selenium contamination.
- Lenses should be cleaned using “LA’s Totally Awesome” cleaning fluid or ordinary hand soap if it is not available.
- After cleaning, lenses should be rinsed with 90% Isopropyl alcohol and then lens degrease (if available).

## Lens Replacement (Gweike : Crackle)

Lens specifications:

Lens Diameter | 20mm
Lens Thickness | ~2mm nominal
Focal Length | >=2.5in (>=63.5mm)

The focal length of the lens for this machine must be greater than or equal to 2.5 inches because the nozzle itself is only 2 inches long. Shorter focal lengths would result in the focal point being inside the nozzle instead of some distance beneath it. 3 inches is recommended because it gives a more generous tolerance for being out of focus (i.e. the focal cone is sharper, meaning it will cut well even when slightly de-focused).

## Lens Replacement (Blue and White: Pop)

Lens specifications:

Lens Diameter | 18mm
Lens Thickness | ~2mm nominal
Focal Length | >=2in (>=63.5mm)

The focal length of the lens for this machine must be greater than or equal to 2 inches because the nozzle itself is only 1.75 inches long. Shorter focal lengths would result in the focal point being inside the nozzle instead of some distance beneath it. 2 inches is recommended because it places the nozzle closer to the work-piece allowing the air-assist to do a better job of pushing air through the nozzle to the work.

# Monthly Inspection

The machine should undergo a monthly inspection wherein the working state should be verified. This process consists of verifying the cleanliness of the optics followed by a set of alignment tests to verify and correct any deviations from the last alignment.

## 1. Inspect and clean optical elements

The first thing to do is to check all 3 mirrors for residue from recent cutting activity. During this inspection, if necessary, clean each of the mirrors with q-tips and “LA’s totally awesome” detergent followed by 97% isopropyl alcohol to ensure that they are clean and free of residue and debris.

Next, the lens should be inspected and cleaned with the same method. Note any pitting or scarring of the lens itself as this could be indicative of damage to the lens from the residue.

As this is being done, if there is more residue than normal, check the operator log sheets to see what has been cut. This may inform future policy on materials, power and speed recommendations.

## 2. Bed level tests

Check to make sure that the bed is still parallel to the gantry. This is done by placing a small block between the nozzle and the bed at each of the 4 corners. The distance should be the same for all 4 corners. If one or more corners are not aligned to within about 1mm, perform the bed level procedure (See Step 2 in the alignment procedures).

For better accuracy, a dial indicator can be mounted to the laser head and the indicator can be run along the bed (with a suitably flat workpiece on the bed). The dial indicator will help align the bed to a much higher precision. In some cases, precision of about 0.25mm (10 thou inches) can be achieved in this way with a little patience.

## 3. Laser beam alignment tests

Next, the beam itself can be checked. Using the Laser Beam Alignment worksheet, fire test pulses using the targets with the laser head at each of the locations shown. This alignment worksheet will help visualize how close the beam is to the center of the apertures. Specifically, the Mirror #3 aperture should have test spots as close as possible to the center and within the aperture hole. If any of the spots are more than 2mm from the center, perform the alignment procedures in steps 4-7 depending on how the spots are mis-aligned. Make sure that the set-screws on the mirrors are tight after alignment so that the alignment does not drift during operation.

## 4. Gantry Square Test

Once the level, optics, and beam have been verified, the machine should be checked as square. This can be done by firing a test pulse at each of the 4 extreme corners of the bed with small pieces of cardboard or other sacrificial medium. The distance between diagonals should be checked to make sure they are equal. If they are not, square the gantry as described in Step 8. Note that this process may upset the alignment of the beam, so if it is found to be out of square, the mirrors may need subsequent alignment.

After all of the alignment tests have been done, file the Laser Beam Alignment worksheet in the folder for the specific machine and note the date and time, your name, and any notes on how you found the condition of the machine to be.

References:

[1] https://smokeandmirrors.store/pages/laser-beam-alignment-guide

[2] https://youtu.be/gCL-B2hnpUc

[3] https://www.youtube.com/watch?v=dyShfEqjyU4

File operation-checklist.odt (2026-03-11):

Industrial Laser Cutter

Operation Checklist

1. Add your name, date, time and material to be cut in the operation log.
2. Obtain key from lockbox with authorized code.
3. Turn on water chiller
4. Turn on power to controller (top switch) on right side of machine. The controller will auto-home the laser head.
5. Place work piece inside cabinet and adjust Z axis to ensure it is below the head.
6. Set origin point for job using arrow buttons and press “Origin” button. Press “Reset” to confirm origin is set to correct location, machine will re-home and return to the origin.
7. Set Z-distance from laser carefully using the green Z up/down buttons. This is normally a 7mm gap between the laser head and work piece although depends on the focal length of the lens. Use the step gauge block to set gap distance.
8. Make sure you know the location of the CO2 extinguisher.
9. CLOSE ALL PANELS to avoid laser exposure.
10. Load job onto machine either through PC or USB stick. Job should never specify a laser power of over 50% because it significantly reduces the life of the laser tube. When cutting jobs, it should be for a RUIDA controller G-code.
11. Open the vent blast gate located on exhaust tube above back of machine.
12. Turn on power to exhaust fans (located near the breaker panel).
13. Turn on air assist (pump/compressor).
14. Verify water temperature is between 16 and 25 degrees C. Top off with distilled water if level is low.
15. Turn on laser power supply (middle switch on right side of machine).
16. Select file and press green “Start/Pause” button to start cutting.
17. When job is finished, remove work piece. Controller will beep when job is finished.
18. Close vent blast gate.
19. Turn off exhaust fans if no other vented equipment is in use.
20. Turn off air assist.
21. Turn off laser tube and controller power.
22. Turn off water chiller.
23. Leave the machine clean: empty chip tray and wipe down residue from cut.
24. Finish filling out job log including all required fields and notes on machine performance.
25. Return lock-out key to lock-box.

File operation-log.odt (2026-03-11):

Machine Operation Log Sheet

Name

Date/Time

Start | End

Material

Power Setting(s) and feed rates (Power/Speed/Type)

Power | Speed | Cut / Engrave
Power | Speed | Cut / Engrave
Power | Speed | Cut / Engrave

Safety Incident (include notes on any flare-ups)

Notes on machine or job performance

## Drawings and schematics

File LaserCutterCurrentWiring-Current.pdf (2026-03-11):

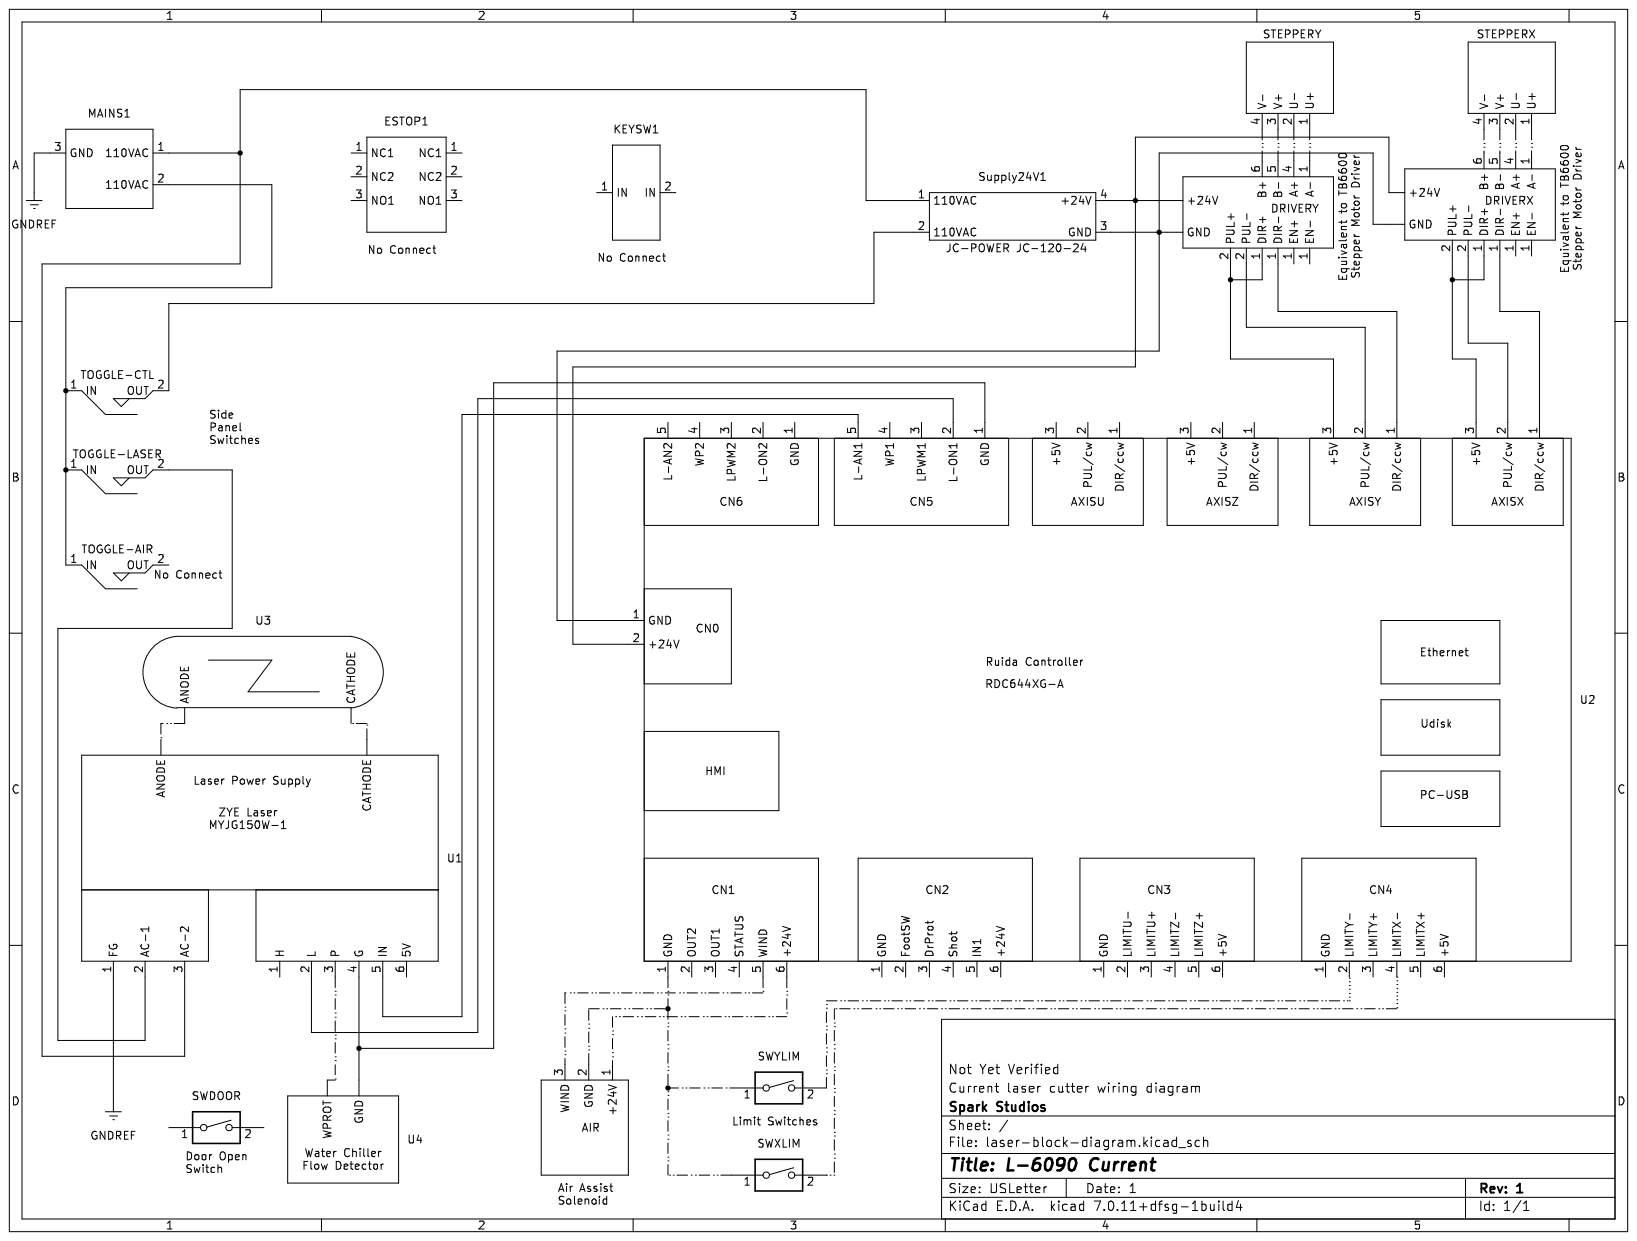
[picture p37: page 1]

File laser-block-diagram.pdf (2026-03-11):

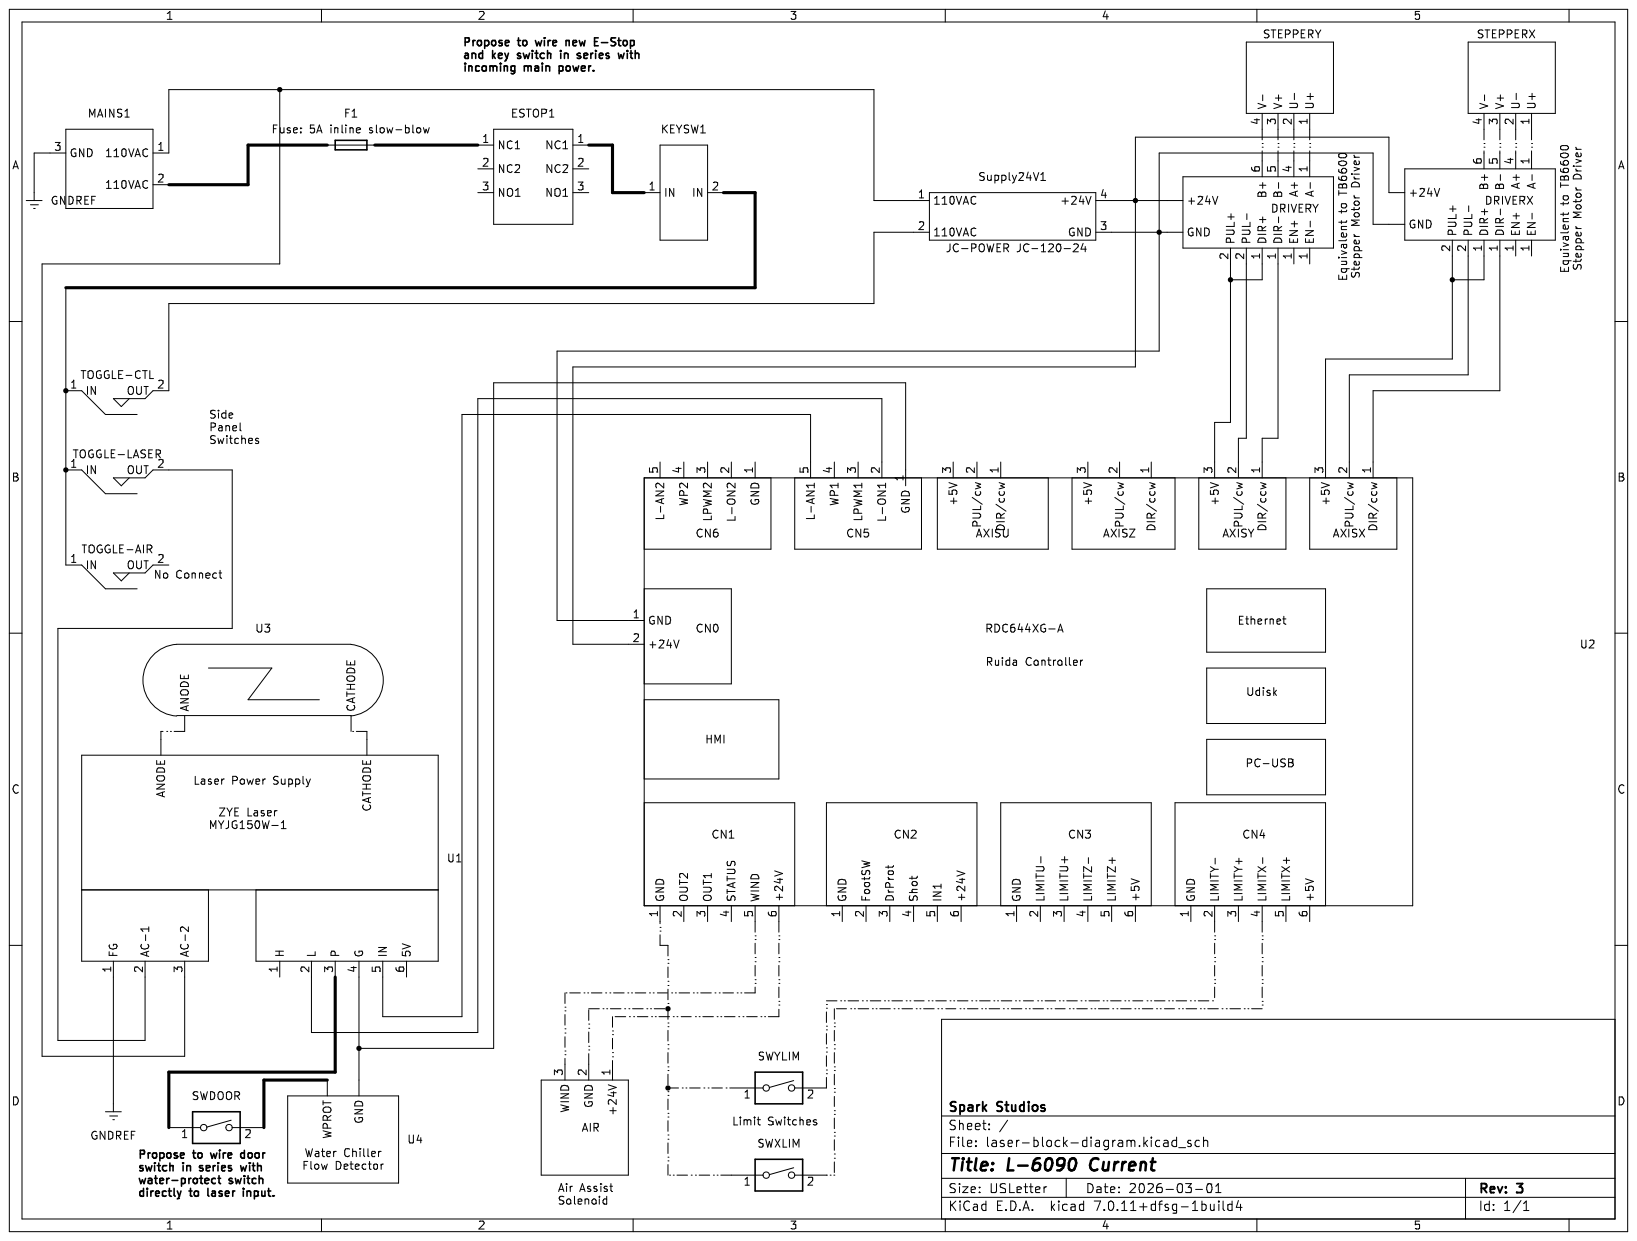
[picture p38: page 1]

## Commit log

2026-03-11 Split documents into separate pdfs.
    [LaserCutterParts.FCStd, laser-block-diagram.kicad_sch]
2026-03-11 Added FreeCAD 3d printed parts.
2026-03-12 Added callibration objects.
    [laser-block-diagram.kicad_sch]
2026-04-19 Updated policy to ban epoxy and fiberglass because of potential clorine gas and/or cyanide emissions.
    [LaserCutterParts-P_AlignmentTarget_Gweike_Mirror3.stl, LaserCutterParts-P_AlignmentTarget_Mirror2.stl, LaserCutterParts-P_AlignmentTarget_Mirror3.stl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]
2026-04-24 Fixed gradient in captain laser logo so hopefully will actually be a proper gradient. Also made the logo a bit more contrasty so we can pick out more details.
2026-04-25 Added lens specifications to alignment guide.
2026-04-27 Added training slides
    [LaserCutterParts.FCStd]
2026-05-07 Added some cutting board stock designs.
2026-05-10 Changed cutting board designs so that the text is rendered as paths instead of text in order to avoid carting fonts around everywhere.
2026-05-25 Updated training materials before first session.
2026-06-02 Updated training materials. Still need to build template stuff.
2026-06-02 Another iteration of the template logic engine. We should use strategy pattern to encapsulate different object type behavior and add an image type, a download button, and a 'theme' selector.
2026-06-04 We now support fonts of lots of different flavor so we can portably cut designs with interesting fonts.
2026-06-05 Added tiny foxtato and some more usability things including hiding hidden layers from lasercut to ensure we don't have extra cruft in the lasercut files.
2026-06-11 We now have selectable fonts, re-named tabs and labels on the share button, and a copy link button (if no images).
2026-06-12 Also fixed a bug where the text bounding-boxes went through to the final cut image.
2026-06-18 Updated training material handouts and slides to be oriented to the SVG template tool.
